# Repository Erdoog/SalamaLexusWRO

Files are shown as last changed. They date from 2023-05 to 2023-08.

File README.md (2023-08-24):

# SalamaLexus Future Engineers WRO 2023
В этом репозитории наша команда собрала все необходимые файлы для документации. Чтобы просмотреть все файлы откройте папки с картинками роботов, 3d моделями, фотографиями команды, а также можете ознакомиться с файлом README, для уточняющей информации.

## Описание файлов и папок документации
``models`` - 3Д модели, разработанные в Fusion360, которые в последующем были распечатаны для использования в нашем роботе

``others`` - файлы необходимые для запуска программы на системной плате робота

``robot-photos`` - 6 фотографий робота

``team-photos`` - 2 фотографии команды (веселая и официальная)

``schemes`` - 2 схемы для сборки робота (электрическая и механическая)

``video`` - видео-обзор от нашей команды на платформе YouTube

``src`` - основная программа (код)

### Коротко о роботе (машинке):
Задний привод работает на моторе. Передняя рулевая ось подключена к серво-моторчику. Два ультразвуковых датчика и камера используются для ориентации на поле. Контрольная система состоит из Control Hub и Arduino nano. Весь корпус был сделан с нуля из фанеры и распечатанных на 3д принтере деталях. (файлы в папке models).

### Мобильность робота (Mobility Management)
>Для нашей команды важно добиться как высокого темпа при заездах, так и пройти все круги максимально аккуратно, чтобы не получить штрафных очков, поэтому робот получился относительно узким у задней оси, что позволит нам допускать меньше ошибок при поворотах и обходах препятствий. Привод робота - задний.

Помимо этого, мы решили убрать лишнее трение с задней оси, так как она неподвижна. Сделали мы это засчет удаления резины, сохраняя ее на передней оси для большего трениия и поворотности!

### Основная система/плата:
Благодаря предыдущему опыту использования, а также легкой интеграции в работу с другими платами (например Ардуино) наш выбор выпал на контрольную систему REV Robotics Control Hub. Данная плата содержит необходимые нам порты для подключения всех моторов и сенсоров, а также энкодеров (счетчики оборотов, проделанных моторами). Позже мы подключили ее к Ардуино Нано для использования дополнительных сенсоров из Ардуино наборов. Схема подключения находится в папке `schemes`

### Выбор моторов:
Наша задача не допустить слишком большой скорости, которую будет тяжело контролировать при объездах препятствий и поворотах, поэтому идеальный RPM (rotations per minute) между 100 и 150, и помимо этого масса не должна быть большой для возможности использовать более объемные аккумуляторы и другие компоненты. В нашей лаборатории были моторы **GoBilda и CoreHEX**. Сравнив характеристики, мы выбрали второй вариант, так как по всем главным сравнительным характеристикам он был намного лучше (125 RPM, Torque 3.2N-m): 



>Для управления передней осью (передними колесами) нет необходимости в отдельном полноценном моторе, поэтому серво-мотор экономит пространство и массу.

Вместо оригинального корпуса мотора мы решили использовать свой, распечатав его на 3д принтере (файл есть в папке  *models*)

### Питание и сенсоры:
Питание не требовало больших значений mAh, но определенно требовало от 11.1В до 12В напряжения, которое нужно для корректной работы контрольный системы (мозга робота), порт XT-30 и небольшой размер батареи был получен с помощью **Li-Po 11.1V 1500mAh**:



*Единственные сенсоры, которые мы использовали это Ардуино ультра-звуковые сенсоры расстояния, а также камеру 720p Logitech для распознования зеленых и красных препятствий. Gyro sensor или же IMU уже встроен в Control Hub, что значительно упрощает процесс подключения дополнительных устройств и сенсоров.*



## Принцип кода
1. Камера, с помощью библиотеки OpenCV определяет кадр и регулярно на протяжении работы всей программы сохраняет данные о том, сколько процентов всех пикселей занимают пиксели красного или зеленого цвета, чтобы узнать какое препятствие из них ближе или дальше.

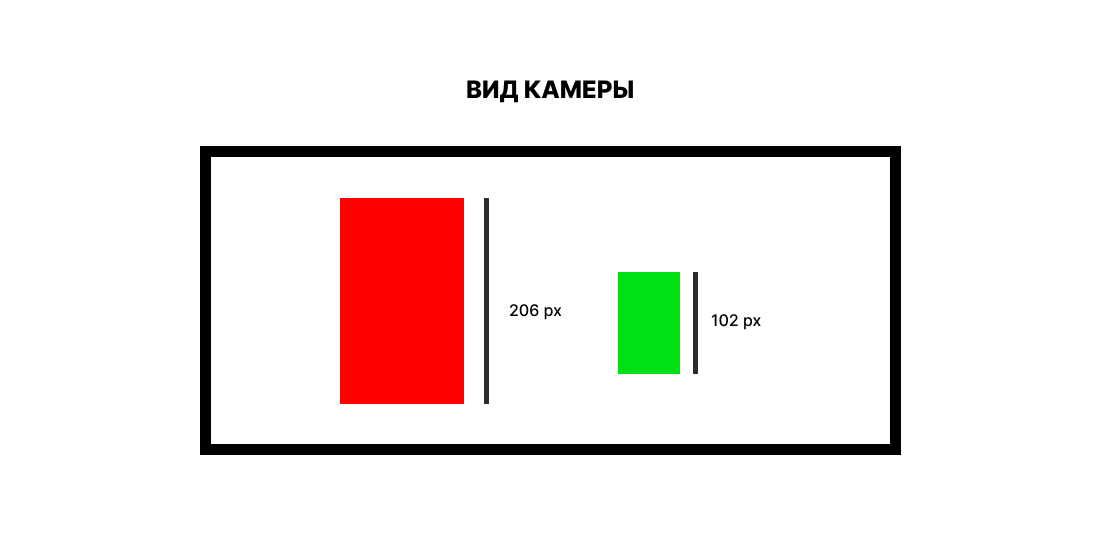
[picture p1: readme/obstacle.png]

   
2. Для построения конкретного движения используется алгоритм "RoadRunner" разработанный на платформе FIRST Tech Challenge и использовать который возможно только при помощи **Android Studio** (читайте ниже как установить Андроид Студио)
Основная идея "RoadRunner" заключается в том, чтобы создать комплексную программу, которая позволяет роботу автоматически и точно выполнять задачи на поле, используя данные из компьютерного зрения и закрытых петель управления. Этот подход может значительно повысить эффективность и надежность автономного периода в соревнованиях. Подробный гайд можно найти на сайте https://learnroadrunner.com/

3. Для определения направления по которому должен двигаться робот, программа отделяет синюю линию от всего остального и смотрит на угол, под которым он лежит. Если угол маленький - то синяя линия ближе. Угол большой - синяя линия дальше, следовательно движение пойдет по часовой стрелке.
   
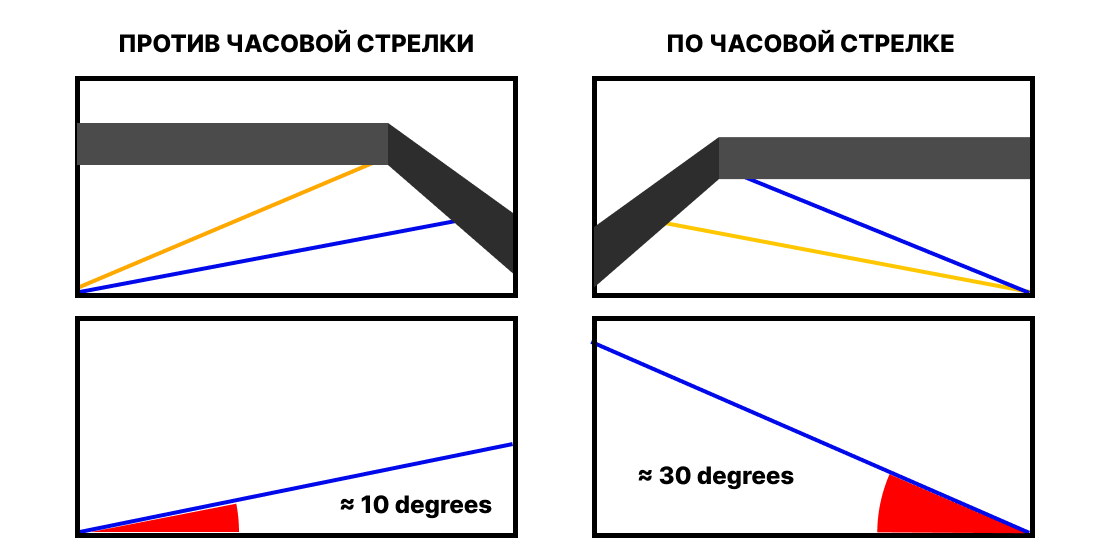
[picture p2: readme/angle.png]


## Установка необходимого ПО для программирования робота
1. Android Studio — это продвинутая интегрированная среда разработки для создания приложений для Android. Этот инструмент является тем же инструментом, который используют профессиональные разработчики приложений для Android. Android Studio рекомендуется для продвинутых пользователей с большим опытом программирования на Java.

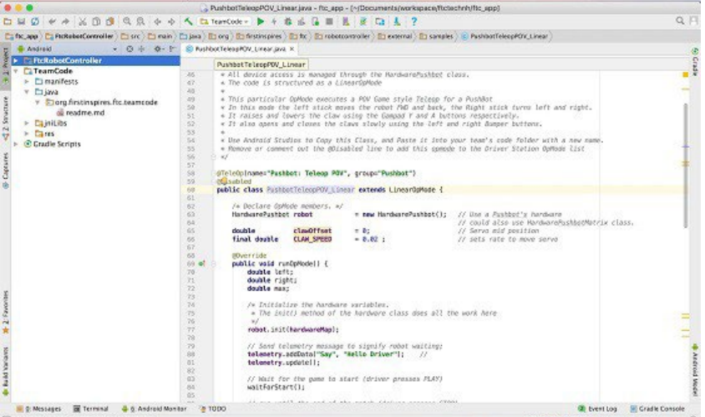
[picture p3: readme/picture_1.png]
2.

Перейдите на сайт андроид-разработчика для загрузки и установки Android Studio:
https://developer.android.com/studio/index.html

3. Нажмите зеленую кнопку «СКАЧАТЬ ANDROID STUDIO», чтобы начать процесс загрузки.
После загрузки установочного пакета запустите приложение и следуйте инструкциям на экране для установки Android Studio.

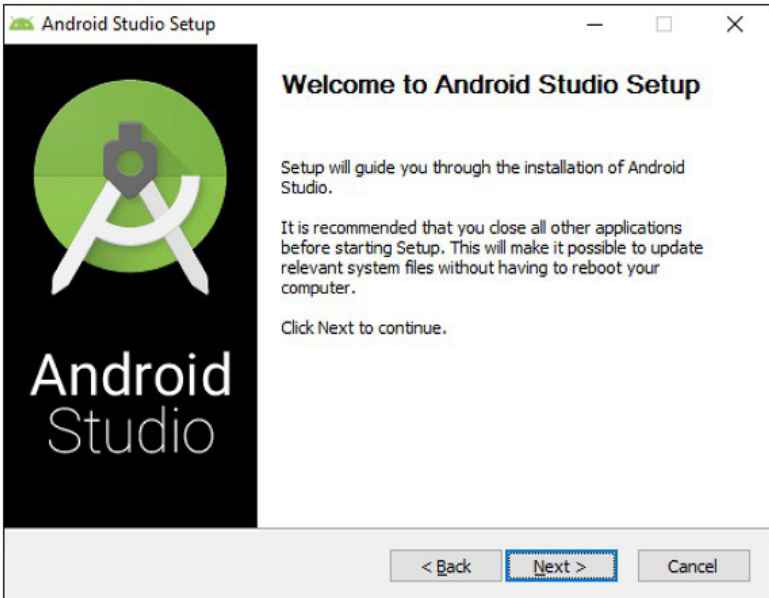
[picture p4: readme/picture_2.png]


4. FTC SDK можно загрузить из репозитория GitHub. GitHub — веб-платформа по контролю версий.
которая позволяет отдельным лицам и организациям размещать контент в Интернете. Чтобы получить доступ к программному обеспечению FTC, вам потребуется публичный репозиторий текущего сезона можно найти по следующему адресу:
https://github.com/FIRST-Tech-Challenge/SkyStone

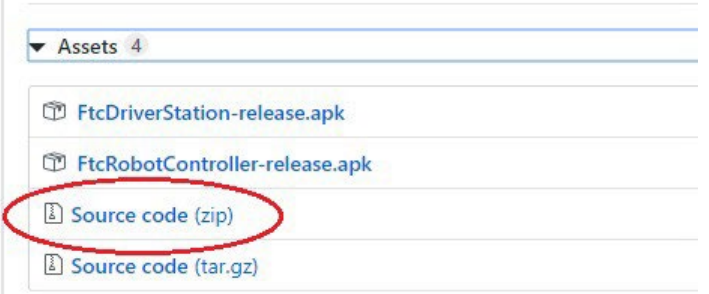
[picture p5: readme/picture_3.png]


5. Чтобы импортировать проект FTC, вам необходимо запустить программное обеспечение Android Studio на вашем компьютере. На главном экране Android Studio выберите параметр «Импортировать проект (Eclipse, ADT, Gradle и т. д.)», чтобы начать процесс импорта.

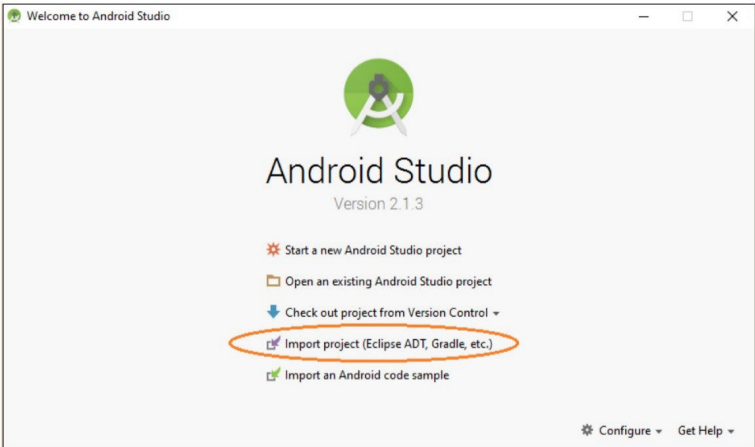
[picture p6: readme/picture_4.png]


6. Android Studio должна предложить вам выбрать папку проекта, которую вы хотите импортировать. Используйте файловый браузер во всплывающем диалоговом окне, чтобы найти и выбрать папку.

7. Убедитесь, что вы выбрали папку извлеченного проекта (а не файл .ZIP, который может иметь имя, похожее на
извлеченная папка). Нажмите кнопку «ОК», чтобы импортировать выбранный проект в Android Studio.

8. Для импорта в Android Studio выбрана папка проекта под названием «SkyStone-5.0». Это
Android Studio может потребоваться несколько минут для импорта проекта.

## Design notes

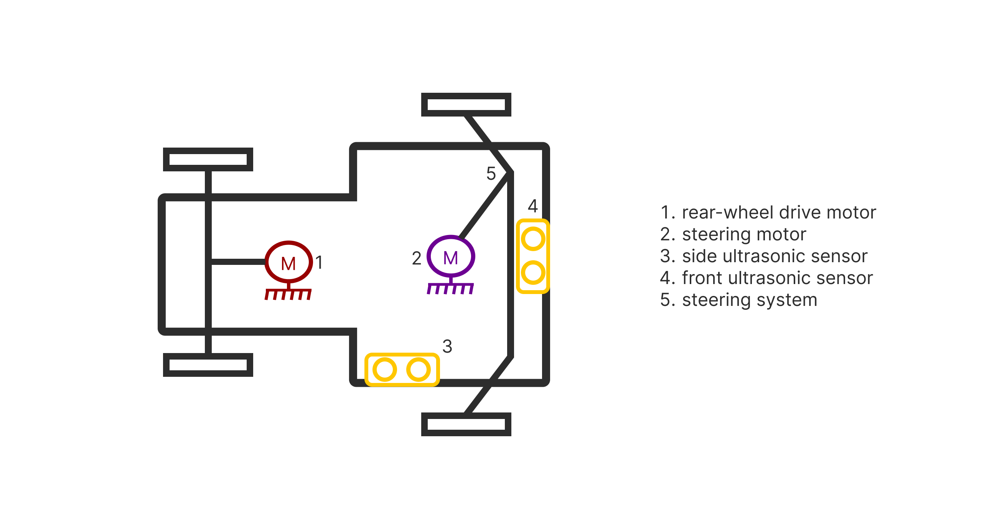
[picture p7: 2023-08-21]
schemes/MechanicalScheme.png

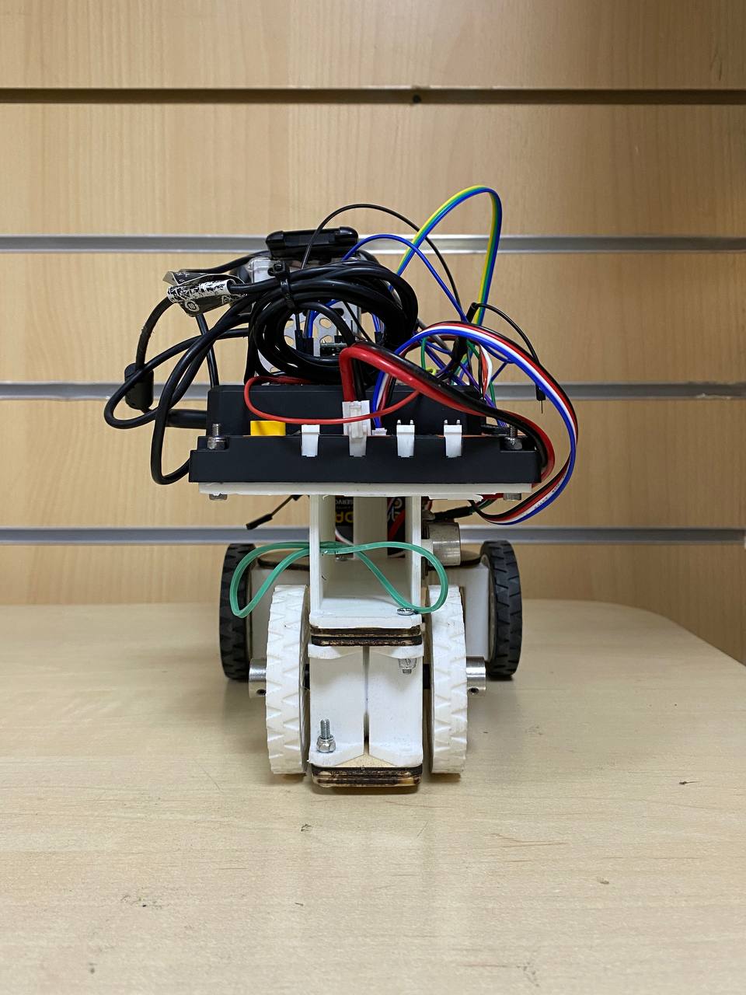
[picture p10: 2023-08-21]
robot-photos/back.jpg

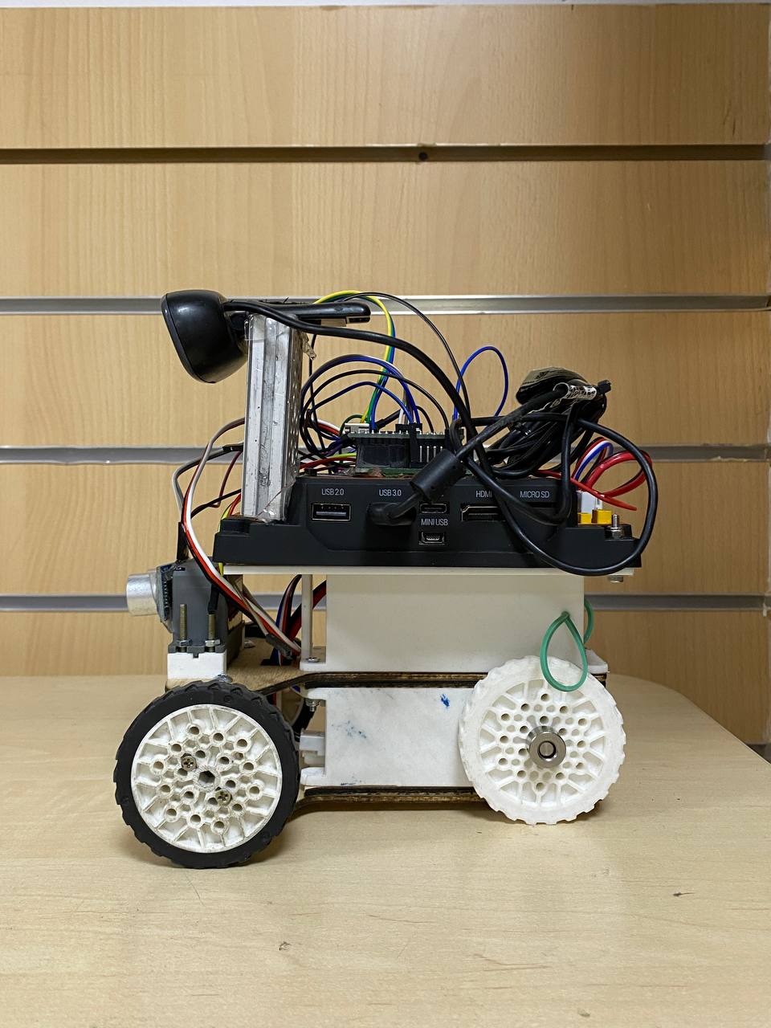
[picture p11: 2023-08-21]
robot-photos/left.jpg

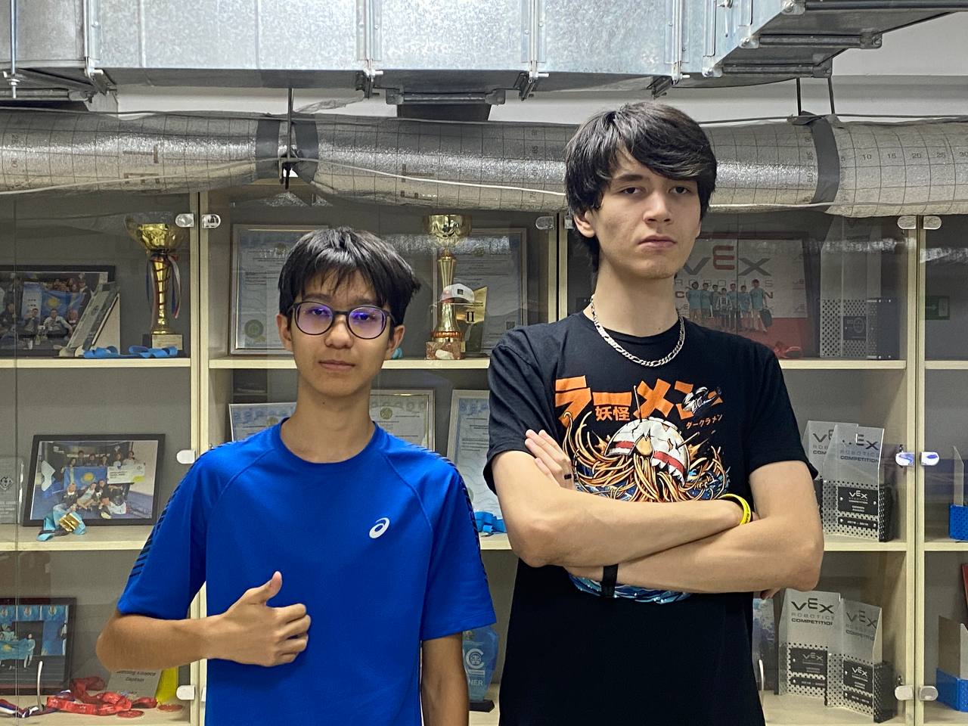
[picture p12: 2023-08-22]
team-photos/tphoto1.jpg

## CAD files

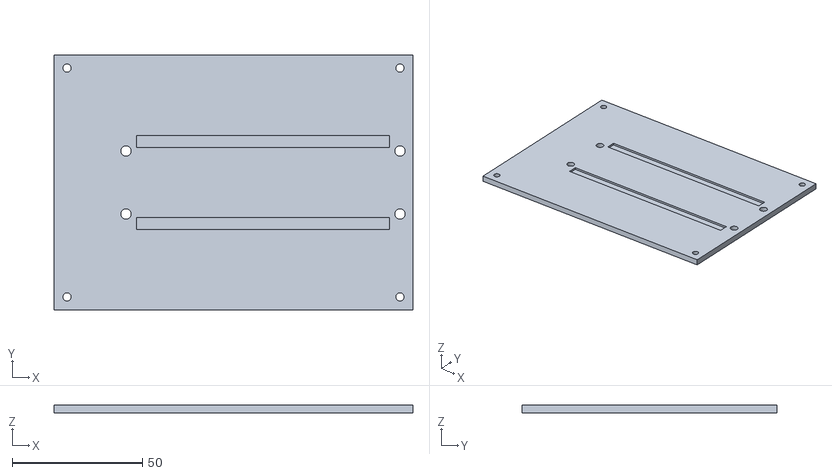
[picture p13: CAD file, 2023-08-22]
models/bata_derj.stl
138.0 x 98.0 x 3.00

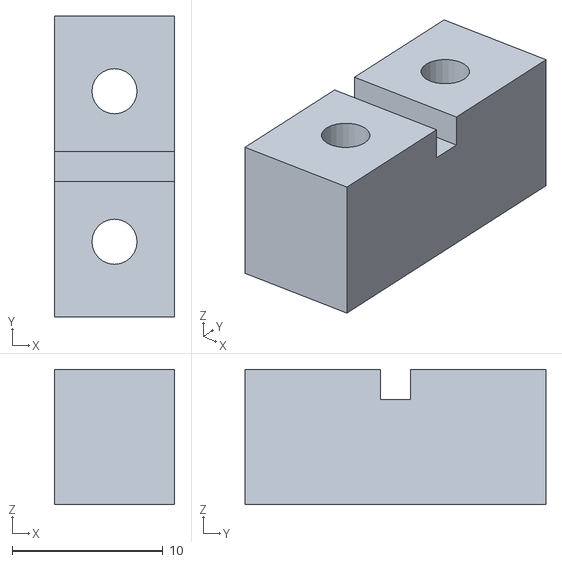
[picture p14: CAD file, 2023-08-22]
models/servo_derj.stl
8.00 x 20.0 x 9.00

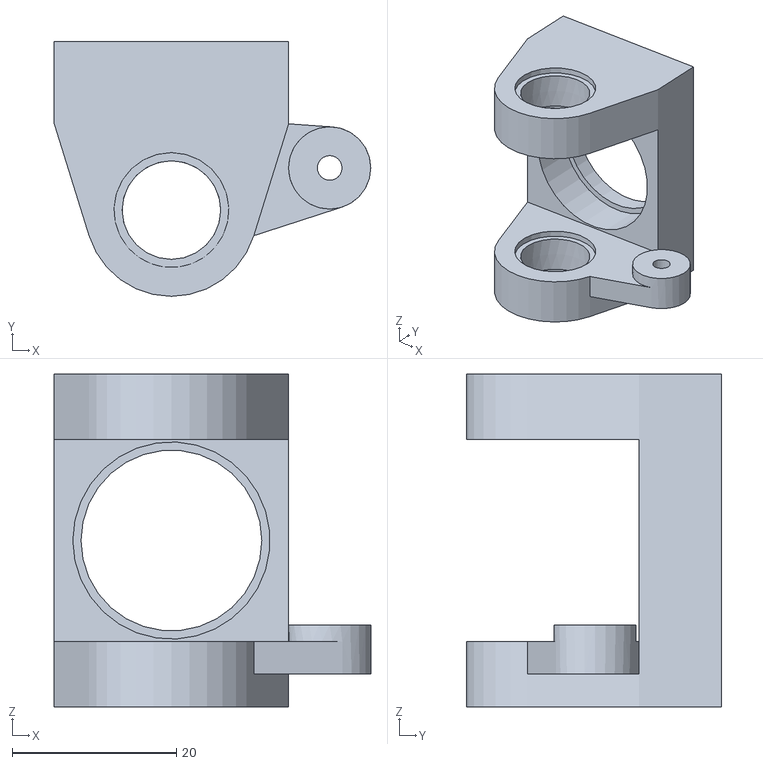
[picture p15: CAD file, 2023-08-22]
models/F_derj_KL_V3.stl
38.5 x 31.0 x 40.5

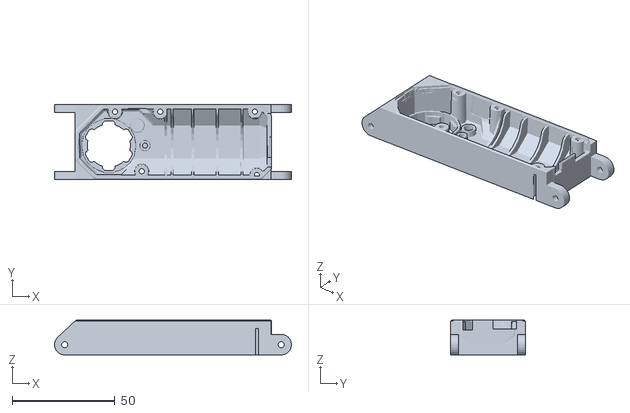
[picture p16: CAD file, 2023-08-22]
models/korpus_L.stl
115.3 x 36.5 x 17.0

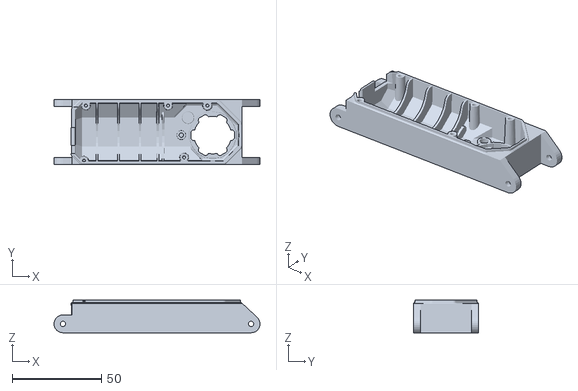
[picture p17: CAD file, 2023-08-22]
models/korpus_R.stl
115.3 x 36.5 x 18.3

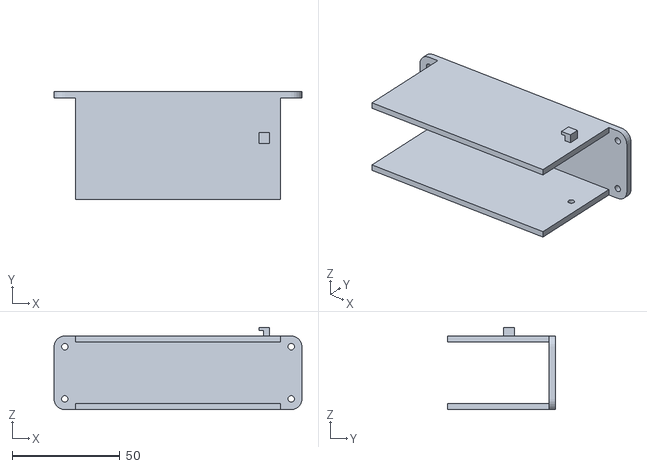
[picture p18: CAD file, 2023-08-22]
models/brain_derj_V2.stl
115.3 x 50.0 x 38.2

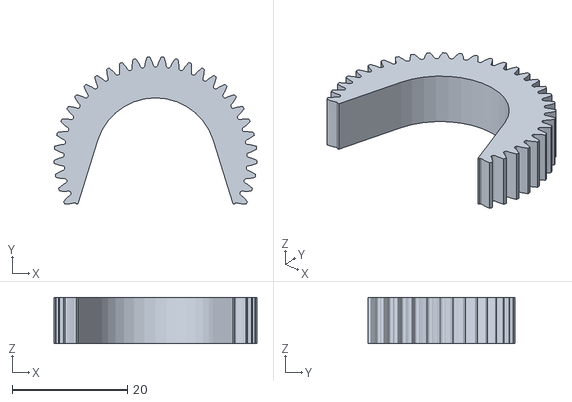
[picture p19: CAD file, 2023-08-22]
models/gear_rul.stl
35.2 x 25.5 x 8.00

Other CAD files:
models/Baza_V3.dwg
models/F_derj_KR_V3.stl

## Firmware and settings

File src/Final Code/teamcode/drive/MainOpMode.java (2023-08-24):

package org.firstinspires.ftc.teamcode.drive;

import com.acmerobotics.dashboard.FtcDashboard;
import com.acmerobotics.dashboard.config.Config;
import com.acmerobotics.roadrunner.geometry.Pose2d;
import com.acmerobotics.roadrunner.geometry.Vector2d;
import com.acmerobotics.roadrunner.trajectory.Trajectory;
import com.qualcomm.robotcore.eventloop.opmode.LinearOpMode;
import com.qualcomm.robotcore.eventloop.opmode.TeleOp;
import com.qualcomm.robotcore.hardware.AnalogInput;
import com.qualcomm.robotcore.util.ElapsedTime;

import org.firstinspires.ftc.teamcode.Detectio.DetectionMaster;
import org.firstinspires.ftc.teamcode.Detectio.DetectionPipeLine;

import java.util.LinkedList;
import java.util.Queue;
import java.util.concurrent.TimeUnit;

@Config
@TeleOp
public class MainOpMode extends LinearOpMode {
    DetectionMaster cvMaster;
    SampleTankDrive drive1;

    Trajectory traj1;

    FtcDashboard dash;
    Color spawnColor = null;

    AnalogInput duino0, duino1, duino2;


    @Override
    public void runOpMode()
    {
        cvMaster = new DetectionMaster(this);
        cvMaster.observe();

        duino0 = hardwareMap.get(AnalogInput.class, "duino0");
        duino1 = hardwareMap.get(AnalogInput.class, "duino1");
        duino2 = hardwareMap.get(AnalogInput.class, "duino2");

        drive1 = new SampleTankDrive(hardwareMap);
        spawns = new LinkedList<>();

        int position = 0;
        int dir = 0;

        while (opModeInInit()) {
            position = getSpawningPosition();
            dir = getDir();

            telemetry.addData("Red", DetectionPipeLine.redArea);
            telemetry.addData("Green", DetectionPipeLine.greenArea);
            telemetry.addData("Analog0", duino0.getVoltage());
            telemetry.addData("Analog1", duino1.getVoltage());
            telemetry.addData("Analog2", duino2.getVoltage());
            telemetry.addData("Filtered Position", position);
            telemetry.addData("Direction", dir);
            telemetry.update();
        }

        Pose2d temporaryStartPose;
        boolean quals = false;

        if (position == 0)
            {
                quals = true;
                temporaryStartPose = newPose2d(80, 3, 90);
            }
            else if (position == 1)
            {
                temporaryStartPose = newPose2d(100, 3, 90);
            }
            else if (position == 2)
            {
                quals = true;
                temporaryStartPose = newPose2d(120, 3, 90);
            }
            else if (position == 3)
            {
                quals = true;
                temporaryStartPose = newPose2d(80, -13, 90);
            }
            else if (position == 4)
            {
                temporaryStartPose = newPose2d(100, -13, 90);
            }
            else
            {
                quals = true;
                temporaryStartPose = newPose2d(120, -13, 90);
            }

            drive1.setPoseEstimate(temporaryStartPose);

            if (quals)
            {
                DriveConstants.MAX_VEL = 20;
                DriveConstants.MAX_ANG_VEL = 2;
                Trajectory afterStartQuals = drive1.trajectoryBuilder(temporaryStartPose)
                        .splineTo(newVector2d(temporaryStartPose.getX() * 2.54, 30), r(90))
                        .build();
                drive1.followTrajectory(afterStartQuals);

                ElapsedTime timer = new ElapsedTime();

                while (timer.time(TimeUnit.SECONDS) < 1.0)
                {
                    getDir();
                }

                if (getDir() == -1)
                {
                    Trajectory loop = drive1.trajectoryBuilder(afterStartQuals.end())
                            .splineTo(newVector2d(120, 100), r(90))

                            .splineTo(newVector2d(100, 120), r(180))
                            .splineTo(newVector2d(-100, 120), r(180))
                            .splineTo(newVector2d(-120, 100), r(270))
                            .splineTo(newVector2d(-120, -100), r(270))
                            .splineTo(newVector2d(-100, -120), r(0))
                            .splineTo(newVector2d(100, -120), r(0))
                            .splineTo(newVector2d(120, -100), r(90))
                            .splineTo(newVector2d(120, 100), r(90))

                            .splineTo(newVector2d(100, 120), r(180))
                            .splineTo(newVector2d(-100, 120), r(180))
                            .splineTo(newVector2d(-120, 100), r(270))
                            .splineTo(newVector2d(-120, -100), r(270))
                            .splineTo(newVector2d(-100, -120), r(0))
                            .splineTo(newVector2d(100, -120), r(0))
                            .splineTo(newVector2d(120, -100), r(90))
                            .splineTo(newVector2d(120, 100), r(90))

                            .splineTo(newVector2d(100, 120), r(180))
                            .splineTo(newVector2d(-100, 120), r(180))
                            .splineTo(newVector2d(-120, 100), r(270))
                            .splineTo(newVector2d(-120, -100), r(270))
                            .splineTo(newVector2d(-100, -120), r(0))
                            .splineTo(newVector2d(100, -120), r(0))
                            .splineTo(newVector2d(120, -100), r(90))
                            .splineTo(newVector2d(120, 0), r(90))
                            .build();
                    drive1.followTrajectory(loop);
                }
                else
                {
                    Pose2d oldPose = drive1.getPoseEstimate();
                    Pose2d newPose = newPose2d(-50 - (150 - oldPose.getX() * 2.54), oldPose.getY(), Math.toDegrees(oldPose.getHeading()));
                    drive1.setPoseEstimate(newPose);

                    Trajectory loop = drive1.trajectoryBuilder(newPose)
                            .splineTo(newVector2d(-120, 100), r(90))

                            .splineTo(newVector2d(-100, 120), r(0))
                            .splineTo(newVector2d(100, 120), r(0))
                            .splineTo(newVector2d(120, 100), r(270))
                            .splineTo(newVector2d(120, -100), r(270))
                            .splineTo(newVector2d(100, -120), r(180))
                            .splineTo(newVector2d(-100, -120), r(180))
                            .splineTo(newVector2d(-120, -100), r(90))
                            .splineTo(newVector2d(-120, 100), r(90))

                            .splineTo(newVector2d(-100, 120), r(0))
                            .splineTo(newVector2d(100, 120), r(0))
                            .splineTo(newVector2d(120, 100), r(270))
                            .splineTo(newVector2d(120, -100), r(270))
                            .splineTo(newVector2d(100, -120), r(180))
                            .splineTo(newVector2d(-100, -120), r(180))
                            .splineTo(newVector2d(-120, -100), r(90))
                            .splineTo(newVector2d(-120, 100), r(90))

                            .splineTo(newVector2d(-100, 120), r(0))
                            .splineTo(newVector2d(100, 120), r(0))
                            .splineTo(newVector2d(120, 100), r(270))
                            .splineTo(newVector2d(120, -100), r(270))
                            .splineTo(newVector2d(100, -120), r(180))
                            .splineTo(newVector2d(-100, -120), r(180))
                            .splineTo(newVector2d(-120, -100), r(90))
                            .splineTo(newVector2d(-120, 0), r(90))
                            .build();

                    drive1.followTrajectory(loop);
                }
                return;
            }

        Trajectory afterStartRed = drive1.trajectoryBuilder(temporaryStartPose)
                .splineTo(newVector2d(130, 53), r(90))
                .splineTo(newVector2d(130, 85), r(90))
                .splineTo(newVector2d(110, 105), r(180))
                .splineTo(newVector2d(100, 105), r(180))
                .build();

        drive1.setPoseEstimate(temporaryStartPose);

        if (getColor() == Color.GREEN)
        {
            Trajectory afterStartGreen = drive1.trajectoryBuilder(temporaryStartPose)
                    .splineTo(newVector2d(75 , 30), r(90))
                    .splineTo(newVector2d(75 , 50), r(90))
                    .splineTo(newVector2d(100, 70), r(0))
                    .splineTo(newVector2d(110, 70), r(0))
                    .splineTo(newVector2d(130, 90), r(90))
                    .splineTo(newVector2d(110, 115), r(180))
                    .splineTo(newVector2d(105, 115), r(180))
                    .build();
            drive1.followTrajectory(afterStartGreen);
        }
        else
        {
            drive1.followTrajectory(afterStartRed);
        }


        if (quals)
        {
            if (dir == -1)
            {


            }
            else
            {

            }
        }

        int lastPos = 0;
        int noneCount = 0;
        for (int zoneNumber = 2; zoneNumber <= 12; zoneNumber++)
        {
            noneCount = 0;
            if (getColor() == Color.GREEN)
            {
                Trajectory firstSegment = drive1.trajectoryBuilder(newPose2d(93, 105, 180))
                        .splineTo(newVector2d(60,87), r(190))
                        .splineTo(newVector2d(2, 87), r(135))
                        .build();
                drive1.followTrajectory(firstSegment);
                Trajectory secondSegment;

                if (getColor() == Color.RED)
                {
//                    secondSegment = drive1.trajectoryBuilder(firstSegment.end())
//                            .splineTo(newVector2d(-50, 135), r(180))
//                            .splineTo(newVector2d(-95, 135), r(180))
//                            .splineTo(newVector2d(-115, 120), r(270))
//                            .splineTo(newVector2d(-115, 110), r(270))
//                            .build();
                    secondSegment = drive1.trajectoryBuilder(newPose2d(2, 90, 180))
                            .splineTo(newVector2d(-20, 111), r(90))
                            .splineTo(newVector2d(-50, 142), r(180))
                            .splineTo(newVector2d(-90, 142), r(180))
                            .splineTo(newVector2d(-107, 123.25), r(270))
                            .splineTo(newVector2d(-107, 113.25), r(270))
                            .build();
                    lastPos = 0;
                }
                else
                {
//                    secondSegment = drive1.trajectoryBuilder(firstSegment.end())uk8q
//                            .splineTo(newVector2d(-5, 95), r(180))
//                            .splineTo(newVector2d(-50, 80), r(180))
//                            .splineTo(newVector2d(-75, 90), r(135))
//                            .splineTo(newVector2d(-107, 123.25), r(270))
//                            .splineTo(newVector2d(-107, 113.25), r(270))
//                            .build();
                    secondSegment = drive1.trajectoryBuilder(newPose2d(2, 90, 180))
                            .splineTo(newVector2d(-50, 90), r(180))
                            .splineTo(newVector2d(-75, 105), r(90))
                            .splineTo(newVector2d(-75, 120), r(90))
                            .splineTo(newVector2d(-90, 142), r(180))
                            .splineTo(newVector2d(-110, 123.25), r(270))
                            .splineTo(newVector2d(-110, 113.25), r(270))
                            .build();
                    lastPos = 1;
                }
                drive1.followTrajectory(secondSegment);
            }
            else
            {
                if (getColor() == Color.NONE)
                    noneCount++;

                Trajectory firstSegment = drive1.trajectoryBuilder(afterStartRed.end())
                        .splineTo(newVector2d(56, 136), r(170))
                        .splineTo(newVector2d(2, 136), r(225))
                        .build();
                drive1.followTrajectory(firstSegment);
                Trajectory secondSegment;
                if (getColor() == Color.GREEN)
                {
//                    secondSegment = drive1.trajectoryBuilder(firstSegment.end())
//                            .splineTo(newVector2d(-50, 80), r(180))
//                            .splineTo(newVector2d(-75, 105), r(90))
//                            .splineTo(newVector2d(-75, 120), r(90))
//                            .splineTo(newVector2d(-95, 140), r(180))
//                            .splineTo(newVector2d(-115, 120), r(270))
//                            .splineTo(newVector2d(-115, 110), r(270))
//                            .build();
                    secondSegment = drive1.trajectoryBuilder(newPose2d(2, 136, 180))
                            .splineTo(newVector2d(-20, 110), r(270))
                            .splineTo(newVector2d(-50, 80), r(180))
                            .splineTo(newVector2d(-75, 105), r(90))
                            .splineTo(newVector2d(-75, 120), r(90))
                            .splineTo(newVector2d(-90, 142), r(180))
                            .splineTo(newVector2d(-112, 123.25), r(270))
                            .splineTo(newVector2d(-112, 113.25), r(270))
                            .build();
//                    secondSegment = drive1.trajectoryBuilder(firstSegment.end())
//                            .splineTo(newVector2d(-5, 95), r(180))
//                            .splineTo(newVector2d(-50, 80), r(180))
//                            .splineTo(newVector2d(-75, 100), r(135))
//                            .splineTo(newVector2d(-107, 123.25), r(270))
//                            .splineTo(newVector2d(-107, 1 13.25), r(270))
//                            .build();
                    lastPos = 2;
                }
                else
                {
                    if (getColor() == Color.NONE)
                        noneCount++;
//                    secondSegment = drive1.trajectoryBuilder(firstSegment.end())
//                            .splineTo(newVector2d(-50, 135), r(180))
//                            .splineTo(newVector2d(-95, 135), r(180))
//                            .splineTo(newVector2d(-115, 120), r(270))
//                            .splineTo(newVector2d(-115, 110), r(270))
//                            .build();
                    secondSegment = drive1.trajectoryBuilder(newPose2d(2, 136, 180))
                            .splineTo(newVector2d(-50, 142), r(180))
                            .splineTo(newVector2d(-90, 142), r(180))
                            .splineTo(newVector2d(-107, 120), r(270))
                            .splineTo(newVector2d(-107, 110), r(270))
                            .build();
                    lastPos = 3;
                }
                drive1.followTrajectory(secondSegment);
            }
            Pose2d lastPose = drive1.getPoseEstimate(), newPose;
            if (lastPos == 0)
            {
                newPose = new Pose2d(lastPose.getY() - 13.25 / 2.54, -lastPose.getX() - 2 / 2.54, lastPose.getHeading() - r(90));
            } else if (lastPos == 1)
            {
                newPose = new Pose2d(lastPose.getY() - 13.25 / 2.54, -lastPose.getX() - 5 / 2.54, lastPose.getHeading() - r(90));
            } else if (lastPos == 2)
            {
                newPose = new Pose2d(lastPose.getY() - 13.25 / 2.54, -lastPose.getX() - 7 / 2.54, lastPose.getHeading() - r(90));
            } else
            {
                newPose = new Pose2d(lastPose.getY() - 10 / 2.54, -lastPose.getX() - 2 / 2.54, lastPose.getHeading() - r(90));
            }
            drive1.setPoseEstimate(newPose);
            if (noneCount == 2)
                break;
        }
        if (noneCount == 2)
        {
            if (dir == -1){
                Trajectory loop = drive1.trajectoryBuilder(drive1.getPoseEstimate())
                        .splineTo(newVector2d(60, 120), r(180))
                        .splineTo(newVector2d(-100, 120), r(180))
                        .splineTo(newVector2d(-120, 100), r(270))
                        .splineTo(newVector2d(-120, -100), r(270))
                        .splineTo(newVector2d(-100, -120), r(0))
                        .splineTo(newVector2d(100, -120), r(0))
                        .splineTo(newVector2d(120, -100), r(90))
                        .splineTo(newVector2d(120, 100), r(90))

                        .splineTo(newVector2d(100, 120), r(180))
                        .splineTo(newVector2d(-100, 120), r(180))
                        .splineTo(newVector2d(-120, 100), r(270))
                        .splineTo(newVector2d(-120, -100), r(270))
                        .splineTo(newVector2d(-100, -120), r(0))
                        .splineTo(newVector2d(100, -120), r(0))
                        .splineTo(newVector2d(120, -100), r(90))
                        .splineTo(newVector2d(120, 100), r(90))

                        .splineTo(newVector2d(100, 120), r(180))
                        .splineTo(newVector2d(-100, 120), r(180))
                        .splineTo(newVector2d(-120, 100), r(270))
                        .splineTo(newVector2d(-120, -100), r(270))
                        .splineTo(newVector2d(-100, -120), r(0))
                        .splineTo(newVector2d(0, -120), r(0))
                        .build();
                drive1.followTrajectory(loop);
            }
            else
            {
                Pose2d oldPose = drive1.getPoseEstimate();
                Pose2d newPose = newPose2d(-50 - (150 - oldPose.getX() * 2.54), oldPose.getY(), Math.toDegrees(oldPose.getHeading()));
                drive1.setPoseEstimate(newPose);

                Trajectory loop = drive1.trajectoryBuilder(newPose)
                        .splineTo(newVector2d(-60, 120), r(0))
                        .splineTo(newVector2d(100, 120), r(0))
                        .splineTo(newVector2d(120, 100), r(270))
                        .splineTo(newVector2d(120, -100), r(270))
                        .splineTo(newVector2d(100, -120), r(180))
                        .splineTo(newVector2d(-100, -120), r(180))
                        .splineTo(newVector2d(-120, -100), r(90))
                        .splineTo(newVector2d(-120, 100), r(90))

                        .splineTo(newVector2d(-100, 120), r(0))
                        .splineTo(newVector2d(100, 120), r(0))
                        .splineTo(newVector2d(120, 100), r(270))
                        .splineTo(newVector2d(120, -100), r(270))
                        .splineTo(newVector2d(100, -120), r(180))
                        .splineTo(newVector2d(-100, -120), r(180))
                        .splineTo(newVector2d(-120, -100), r(90))
                        .splineTo(newVector2d(-120, 100), r(90))

                        .splineTo(newVector2d(-100, 120), r(0))
                        .splineTo(newVector2d(100, 120), r(0))
                        .splineTo(newVector2d(120, 100), r(270))
                        .splineTo(newVector2d(120, -100), r(270))
                        .splineTo(newVector2d(100, -120), r(180))
                        .splineTo(newVector2d(0, -120), r(180))
//                        .splineTo(newVector2d(-120, -100), r(90))
//                        .splineTo(newVector2d(-120, 0), r(90))
                        .build();

                drive1.followTrajectory(loop);
            }
        }
    }


    Queue<Double> spawns;

    private int getSpawningPosition()
    {
        int b0 = (duino0.getVoltage() > 2.5 ? 1 : 0);
        int b1 = (duino1.getVoltage() > 2.5 ? 1 : 0);
        int b2 = (duino2.getVoltage() > 2.5 ? 1 : 0);
        double position = b0 + b1 * 2 + b2 * 4;

        spawns.add(position);
        if (spawns.size() > 1000) {
            spawns.remove();
        }

        int[] c = {0, 0, 0, 0, 0, 0};

        for (double spw : spawns)
        {
            if (spw == 0)
                c[0]++;
            if (spw == 1)
                c[1]++;
            if (spw == 2)
                c[2]++;
            if (spw == 3)
                c[3]++;
            if (spw == 4)
                c[4]++;
            if (spw == 5)
                c[5]++;
        }

        int biggestId = 0;

        for (int spwId = 0; spwId < 6; spwId++)
        {
            if (c[spwId] > c[biggestId])
                biggestId = spwId;
        }

        return biggestId;
    }

    int direction = 0;
    Queue<Double> angles = new LinkedList<>();
    private double getAng()
    {
        angles.add(DetectionPipeLine.blueLineAngle);
        if (angles.size() > 20) {
            angles.remove();
        }
        double accumAngle = 0;
        for (double angle : angles)
        {
            accumAngle += angle;
        }
        accumAngle /= angles.size();
        return accumAngle;
    }

    private int getDir()
    {
        double ang = getAng();
        if (ang == 90)
        {
            return 0;
        }
        if (ang > -5)
        {
            return -1;
        }
        return 1;
    }

    public static int minimalAreaThreshold = 3000 ;
    private Color getColor()
    {
        if (DetectionPipeLine.redArea > minimalAreaThreshold
         && DetectionPipeLine.greenArea > minimalAreaThreshold)

            return (DetectionPipeLine.greenArea > DetectionPipeLine.redArea ?
                    Color.GREEN : Color.RED);
        if (DetectionPipeLine.greenArea > minimalAreaThreshold)
            return Color.GREEN;
        if (DetectionPipeLine.redArea > minimalAreaThreshold)
            return Color.RED;
        return Color.NONE;
    }
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

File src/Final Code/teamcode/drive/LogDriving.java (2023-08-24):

package org.firstinspires.ftc.teamcode.drive;

import com.acmerobotics.dashboard.config.Config;
import com.acmerobotics.roadrunner.geometry.Pose2d;
import com.qualcomm.robotcore.eventloop.opmode.OpMode;
import com.qualcomm.robotcore.eventloop.opmode.TeleOp;
import com.qualcomm.robotcore.hardware.DcMotor;
import com.qualcomm.robotcore.hardware.DcMotorEx;
import com.qualcomm.robotcore.hardware.DcMotorSimple;
import com.qualcomm.robotcore.hardware.Servo;

@TeleOp
@Config
public class LogDriving extends OpMode {
    DcMotorEx leftMotor;
    DcMotorEx rightMotor;
    Servo steer;

    @Override
    public void init()
    {
        leftMotor = hardwareMap.get(DcMotorEx.class, "left_drive");
        rightMotor = hardwareMap.get(DcMotorEx.class,   "right_drive");

        steer = hardwareMap.get(Servo.class, "steer");

        rightMotor.setDirection(DcMotorSimple.Direction.REVERSE);

        rightMotor.setZeroPowerBehavior(DcMotor.ZeroPowerBehavior.BRAKE);
        leftMotor.setZeroPowerBehavior(DcMotor.ZeroPowerBehavior.BRAKE);

        rightMotor.setMode(DcMotor.RunMode.RUN_WITHOUT_ENCODER);
        leftMotor.setMode(DcMotor.RunMode.RUN_WITHOUT_ENCODER);

        drive = new SampleTankDrive(hardwareMap);
    }

    //    public static double steerMulti = -0.11;
    public static double steerMulti = 0.4;
    public static double speed = 1;
    public static double zeroSteer = 0.55;

    SampleTankDrive drive;

    @Override
    public void loop()
    {
        double forwardPower = Math.pow(gamepad1.right_trigger, 3) - Math.pow(gamepad1.left_trigger, 3);
        double rotationalPower = Math.pow(gamepad1.left_stick_x, 2) * (gamepad1.left_stick_x > 0 ? 1.0 : -1.0);

        drive.setDrivePower(new Pose2d(forwardPower, 0, rotationalPower));
        telemetry.addData("turn", drive.outputable);
        telemetry.update();
    }
}

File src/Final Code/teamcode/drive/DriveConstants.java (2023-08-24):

package org.firstinspires.ftc.teamcode.drive;

import com.acmerobotics.dashboard.config.Config;
import com.qualcomm.hardware.rev.RevHubOrientationOnRobot;
import com.qualcomm.robotcore.hardware.PIDFCoefficients;

@Config
public class DriveConstants {

    /*
     * These are motor constants that should be listed online for your motors.
     */
    public static double TICKS_PER_REV = 288;
    public static double MAX_RPM = 125;

    /*
     * Set RUN_USING_ENCODER to true to enable built-in hub velocity control using drive encoders.
     * Set this flag to false if drive encoders are not present and an alternative localization
     * method is in use (e.g., tracking wheels).
     *
     * If using the built-in motor velocity PID, update MOTOR_VELO_PID with the tuned coefficients
     * from DriveVelocityPIDTuner.
     */
    public static final boolean RUN_USING_ENCODER = false;
    public static PIDFCoefficients MOTOR_VELO_PID = new PIDFCoefficients(0, 0, 0,
            getMotorVelocityF(MAX_RPM / 60 * TICKS_PER_REV));

    /*
     * These are physical constants that can be determined from your robot (including the track
     *
     * width; it will be tune empirically later although a rough estimate is important). Users are
     * free to chose whichever linear distance unit they would like so long as it is consistently
     * used. The default values were selected with inches in mind. Road runner uses radians for
     * angular distances although most angular parameters are wrapped in Math.toRadians() for
     * convenience. Make sure to exclude any gear ratio included in MOTOR_CONFIG from GEAR_RATIO.
     */
    public static double WHEEL_RADIUS = 2.3622;//gear ratio 1.2692 prev
    public static double GEAR_RATIO = 1; // output (wheel) speed / input (motor) speed
    public static double TRACK_WIDTH = 18; // in

    /*
     * These are the feedforward parameters used to model the drive motor behavior. If you are using
     * the built-in velocity PID, *these values are fine as is*. Howeve/'r, if you do not have drive
     * motor encoders or have elected not to use them for velocity control, these values should be
     * empirically tuned.
     */
//    public static double kV = 0.0115;
//    public static double kA = 0.0025;
//    public static double kStatic = 0.001;

    public static double kV = 0.01;
    public static double kA = 0.001;
    public static double kStatic = 0.001;

    /*
     * These values are used to generate the trajectories for you robot. To ensure proper operation,
     * the constraints should never exceed ~80% of the robot's actual capabilities. While Road
     * Runner is designed to enable faster autonomous motion, it is a good idea for testing to start
     * small and gradually increase them later after everything is working. All distance units are
     * inches.
     */
    /*
     * Note from LearnRoadRunner.com:
     * The velocity and acceleration constraints were calculated based on the following equation:
     * ((MAX_RPM / 60) * GEAR_RATIO * WHEEL_RADIUS * 2 * Math.PI) * 0.85
     * Resulting in 94.61891165582561 in/s.
     * This is only 85% of the theoretical maximum velocity of the bot, following the recommendation above.
     * This is capped at 85% because there are a number of variables that will prevent your bot from actually
     * reaching this maximum velocity: voltage dropping over the game, bot weight, general mechanical inefficiencies, etc.
     * However, you can push this higher yourself if you'd like. Perhaps raise it to 90-95% of the theoretically
     * max velocity. The theoretically maximum velocity is 111.31636665391248 in/s.
     * Just make sure that your bot can actually reach this maximum velocity. Path following will be detrimentally
     * affected if it is aiming for a velocity not actually possible.
     *
     * The maximum acceleration is somewhat arbitrary and it is recommended that you tweak this yourself based on
     * actual testing. Just set it at a reasonable value and keep increasing until your path following starts
     * to degrade. As of now, it simply mirrors the velocity, resulting in 94.61891165582561 in/s/s
     *
     * Maximum Angular Velocity is calculated as: maximum velocity / trackWidth * (180 / Math.PI) but capped at 360°/s.
     * You are free to raise this on your own if you would like. It is best determined through experimentation.
     *
     * WARNING: LearnRoadRunner.com's constant generator has capped the calculated recommended velocity at 90in/s.
     * This message is showing because your gear ratio/motor RPM/etc. configuration, results in a recommended
     * velocity (85% of max velocity) exceeding 90in/s.
     * (Your recommended velocity was 94.61891165582561in/s)
     * This is simply insanely fast for an FTC bot and chances are your bot cannot properly reach these speeds.
     *
     * Just to be safe, LearnRoadRunner.com has arbitrarily limited your velocity to 90in/s.
     * You are free to increase it yourself. If you do run into issues, please lower the maximum velocity.
     *
     * A documented case of a similar error which served as an impetus for this reasoning can be found here:
     * https://github.com/acmerobotics/road-runner-quickstart/issues/91

     */
    public static double MAX_VEL = 17;
    public static double MAX_ACCEL = 10;
    public static double MAX_ANG_VEL = 1.5;
    public static double MAX_ANG_ACCEL = 1.5;

    public static RevHubOrientationOnRobot.LogoFacingDirection LOGO_FACING_DIR =
            RevHubOrientationOnRobot.LogoFacingDirection.UP;
    public static RevHubOrientationOnRobot.UsbFacingDirection USB_FACING_DIR =
            RevHubOrientationOnRobot.UsbFacingDirection.LEFT;
//    public static RevHubOrientationOnRobot.LogoFacingDirection LOGO_FACING_DIR =
//            RevHubOrientationOnRobot.LogoFacingDirection.FORWARD;
//    public static RevHubOrientationOnRobot.UsbFacingDirection USB_FACING_DIR =
//            RevHubOrientationOnRobot.UsbFacingDirection.LEFT;


    public static double encoderTicksToInches(double ticks) {
        return WHEEL_RADIUS * 2 * Math.PI * GEAR_RATIO * ticks / TICKS_PER_REV;
    }

    public static double rpmToVelocity(double rpm) {
        return rpm * GEAR_RATIO * 2 * Math.PI * WHEEL_RADIUS / 60.0;
    }

    public static double getMotorVelocityF(double ticksPerSecond) {
        // see https://docs.google.com/document/d/1tyWrXDfMidwYyP_5H4mZyVgaEswhOC35gvdmP-V-5hA/edit#heading=h.61g9ixenznbx
        return 32767 / ticksPerSecond;
    }
}

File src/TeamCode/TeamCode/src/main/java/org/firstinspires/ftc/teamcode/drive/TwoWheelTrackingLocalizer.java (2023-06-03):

package org.firstinspires.ftc.teamcode.drive;

import androidx.annotation.NonNull;

import com.acmerobotics.roadrunner.geometry.Pose2d;
import com.acmerobotics.roadrunner.localization.TwoTrackingWheelLocalizer;
import com.qualcomm.robotcore.hardware.DcMotorEx;
import com.qualcomm.robotcore.hardware.HardwareMap;

import org.firstinspires.ftc.teamcode.util.Encoder;

import java.util.Arrays;
import java.util.List;

/*
 * Sample tracking wheel localizer implementation assuming the standard configuration:
 *
 *    ^
 *    |
 *    | ( x direction)
 *    |
 *    v
 *    <----( y direction )---->
 *        (forward)
 *    /--------------\
 *    |     ____     |
 *    |     ----     |    <- Perpendicular Wheel
 *    |           || |
 *    |           || |    <- Parallel Wheel
 *    |              |
 *    |              |
 *    \--------------/
 *
 */
public class TwoWheelTrackingLocalizer extends TwoTrackingWheelLocalizer {
    public static double TICKS_PER_REV = 288;
    public static double WHEEL_RADIUS = 1.77; // in
    public static double GEAR_RATIO = 1; // output (wheel) speed / input (encoder) speed

    public static double PARALLEL_X = 0; // X is the up and down direction
    public static double PARALLEL_Y = 0; // Y is the strafe direction

    // Parallel/Perpendicular to the forward axis
    // Parallel wheel is parallel to the forward axis
    // Perpendicular is perpendicular to the forward axis
    private Encoder parallelEncoder;

    private SampleTankDrive drive;

    public TwoWheelTrackingLocalizer(HardwareMap hardwareMap, SampleTankDrive drive) {
        super(Arrays.asList(
                new Pose2d(PARALLEL_X, PARALLEL_Y, 0),
                new Pose2d(0, 0, Math.toRadians(90))
        ));
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

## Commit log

2023-05-03 Initialized project
    [app_settings.xml]
2023-08-21 change files layout
    [app_settings.xml]
